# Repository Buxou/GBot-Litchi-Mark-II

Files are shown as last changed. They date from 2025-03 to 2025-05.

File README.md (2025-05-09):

# GBot-Litchi-Mark-II

Продолжение линейки Litchi – Litchi Mark II. 

[3D-моделька, чтобы покрутить.](https://myhub.autodesk360.com/ue2ddbd59/g/shares/SH286ddQT78850c0d8a4284d03fa6811be10?mode=embed)

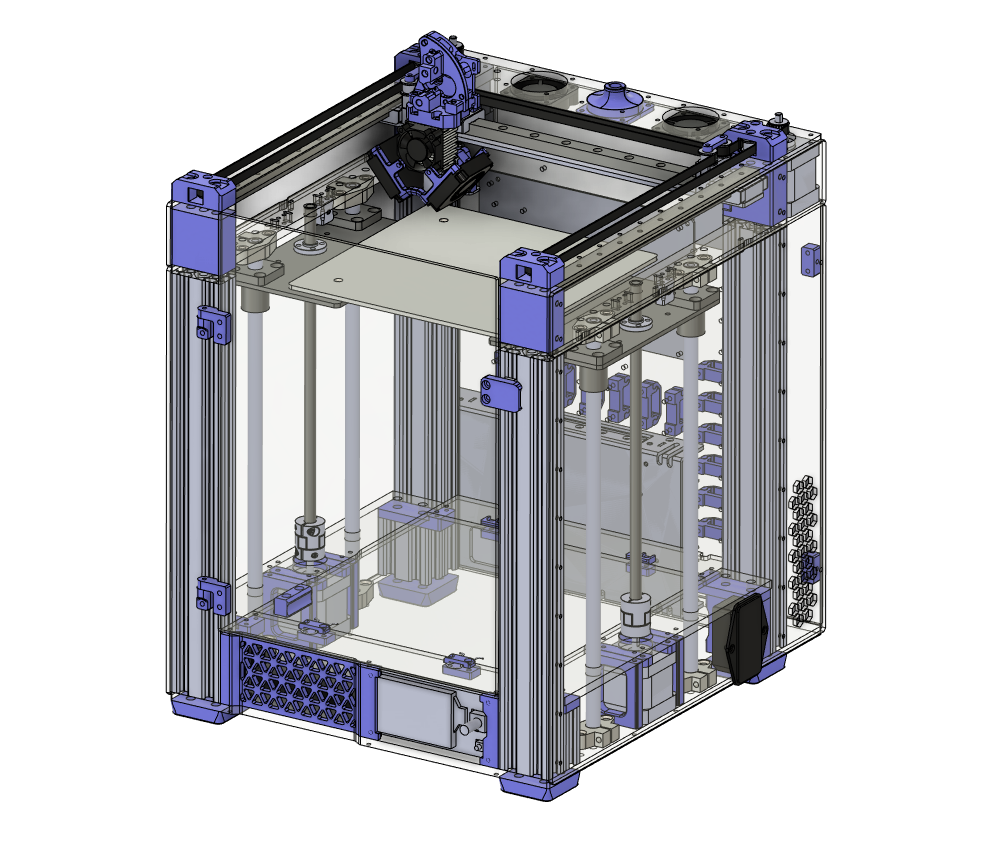
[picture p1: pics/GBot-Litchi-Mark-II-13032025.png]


## Особенности и характеристики:

- Поле 180х180х180 мм
- Габариты 340х306х420 мм
- Кинематика HBot (в перспективе CoreXY)
- Подача direct (аналог Sailfin)
- Перемещение XY – рельсы
- Перемещение Z – валы
- Датчики Холла в качестве концевиков
- Два отсека электроники: подвал/рюкзак
- Доступ к подвалу не требует переворачивания принтера
- Охлаждение рюкзака (заднего отсека) пассивное + активное
- Dual Z выравнивание сторон по концевикам
- Автокалибровка стола датчиком Beacon (карта высот)

## Корпус

Основан на констуркционном профиле 2040. Кинематика расположена на 6мм акриле, обшивка 3мм. Есть возможность установки купола, т.е. полностью закрытый корпус – пассивную термокамеру (в разработке).

## Метизы
- м6х30    8шт снизу в ножки в профиль.
- м6х18    8шт снизу в ножки в маленькие огрызки профиля\печатные детали.
- м6х85\90    8шт сверху в крепления шкивов, 85мм при верхнем портале 6мм и 90мм при верхнем портале 8мм.
- м3х10    20шт для крепления нижних правой и левой панели.
- м3х10    8шт для крепления верхних правой и левой панели.
- м3х10    14шт для крепления передней печатной панели и акриловой детали над ней и печатных деталей к ней.
- м3х10    8шт для крепления акриловой панели внутри принтера у задней стенки и крепления к ней печатных деталей для акрилового капота.
- м3х16    8шт для крепления моторов по Z.
- м3х65\70    4шт для крепления стоек рядом с моторами Z, либо переделать детали под вплавляемые гайки. Как вариант вкрутить в пластик или использовать саморезы.
- м3х10    8шт для крепления моторов на верхний портал.
- м3х20    6шт для крепления шкивов в печатных деталях по углам.
- м3х12    20шт для крепления рельс по Y.
- м3х8\10    9шт для крепления рельсы по Х, винты с длинной 10мм выглядят более надежно ибо "мяса в рельсе 3.5мм и 3мм балка Х.
- м3х8\10    4шт для крепления головы к рельсе Х при толщине верхнего портала 6мм. Толщина кронштейна в месте крепления 6мм и глубина резьбы в каретке 3.5мм, лучше взять винты длиной 10мм и проложить шайбы.
- м3х10\12    4шт для крепления головы к рельсе Х при верхрем портале в 8мм. Толщина кронштейна в месте крепления 8мм и глубина резьбы в каретке 3.5мм, лучше взять винты длиной 12мм и проложить шайбы.
- м3х6    8шт для крепления балки Х к кареткам рельс Y.
- м3х20    3шт для крепления вентилятора обдува драйверов.
- м5х16\20    16шт для крепления держателей валов оси Z. Длина 16мм для держателей валов с "тонкими ушами" в 5мм, для держаталей с толстыми ушами 20мм.

- Осторожно могут быть ошибки, просьба сверяться с 3д моделью. Позже допишу.

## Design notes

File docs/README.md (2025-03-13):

## Содержание данной секции:

(ещё не готово) **[BOM GBot Litchi Mark II.md](BOM_GBot_Litchi_Mark_II.md)** — список комплектующих

(ещё не готово) **[Fixings BOM GBot Litchi Mark II.md](Fixings_BOM_GBot_Litchi_Mark_II.md)** — расширенный список "болтов, винтов и гаек"

**[Datasheet A3144.pdf](Datasheet_A3144.pdf)** — документация на датчики Холла А3144, которые используются как концевики

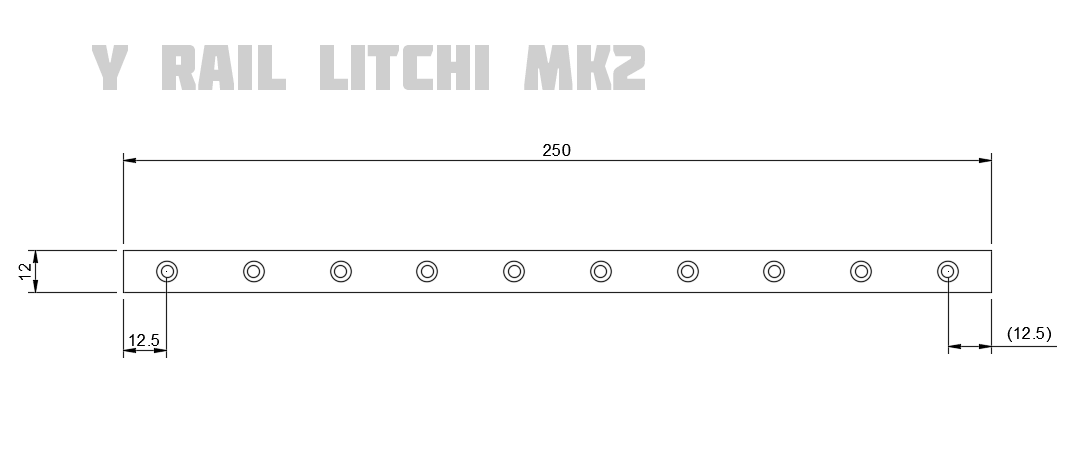
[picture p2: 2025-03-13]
docs/drawings/Y_Rail_GBot_Litchi_Mk2.png

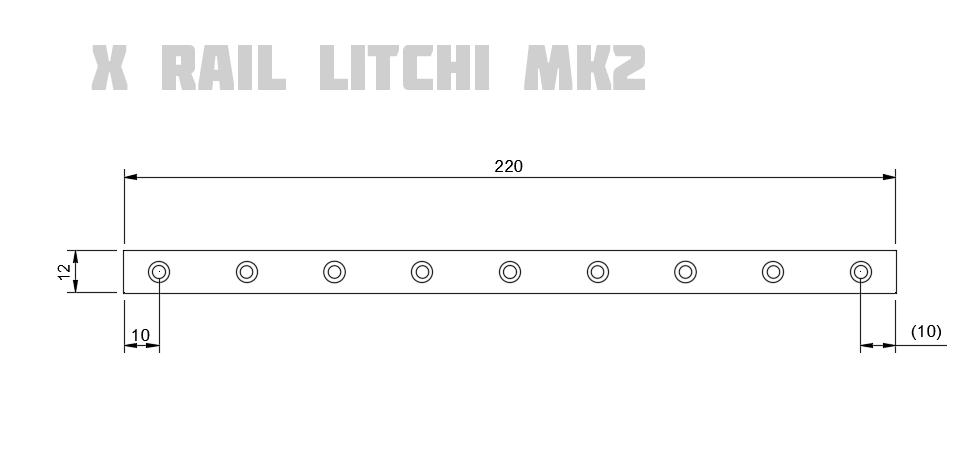
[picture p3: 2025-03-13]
docs/drawings/X_Rail_GBot_Litchi_Mk2.png

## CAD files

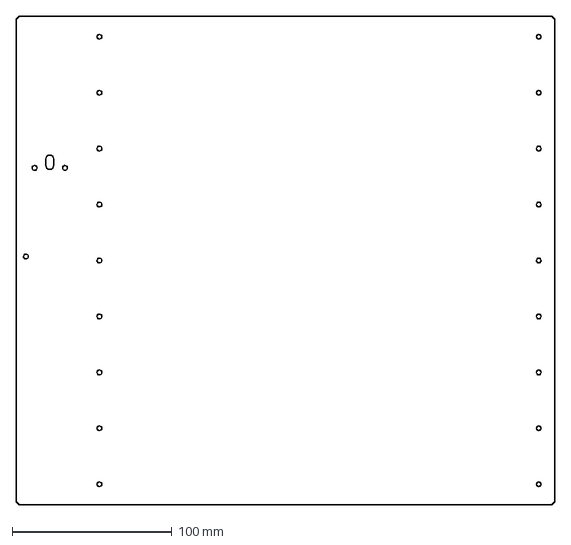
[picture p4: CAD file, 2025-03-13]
CAD/DXF/leftPanelBottom GBtLitchiMII.DXF
337.0 x 306.0 mm

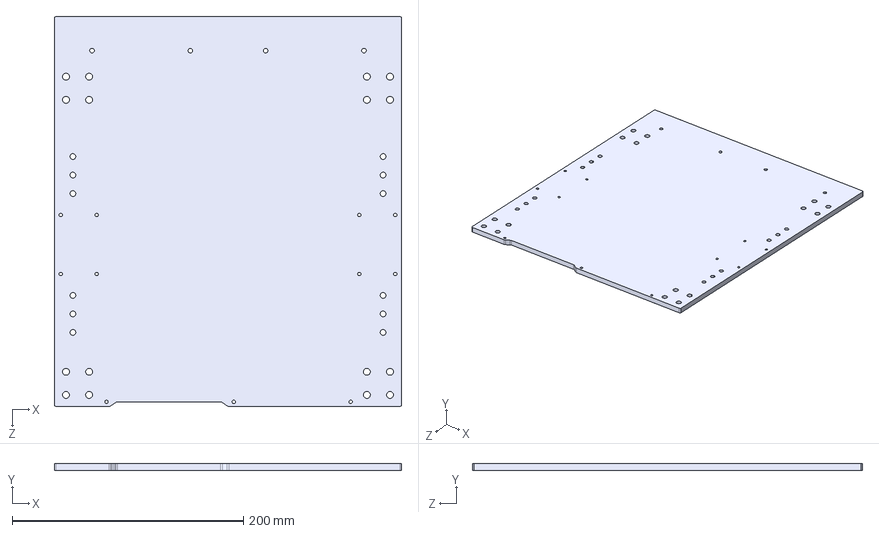
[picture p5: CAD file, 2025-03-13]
CAD/STEP/bottomPlate GBtLitchiMII.STEP
300.0 x 6.00 x 337.0 mm

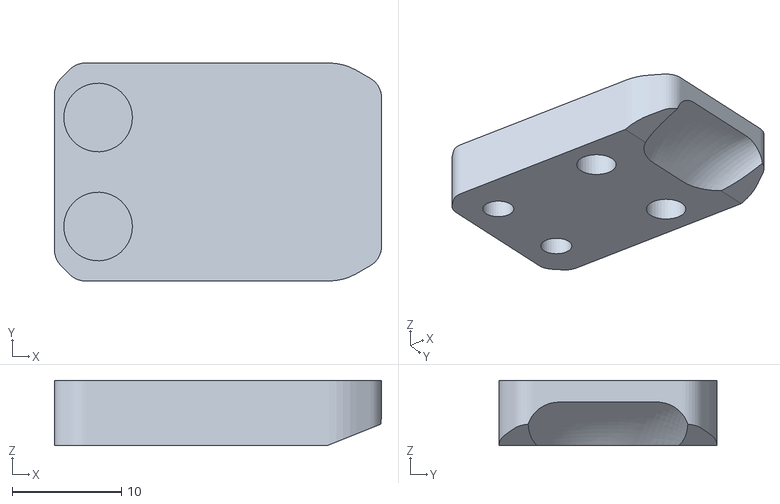
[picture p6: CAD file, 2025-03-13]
CAD/STL/doorHandle GBtLitchiMII.STL
30.0 x 20.0 x 6.00

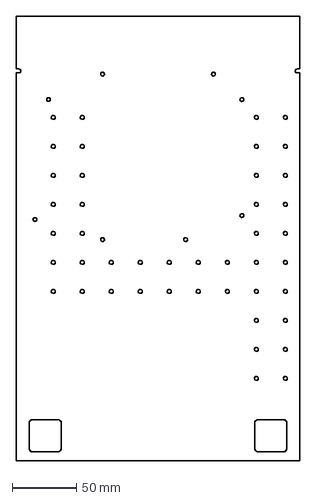
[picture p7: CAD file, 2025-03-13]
CAD/DXF/backPanel GBtLitchiMII.DXF
220.0 x 345.0 mm

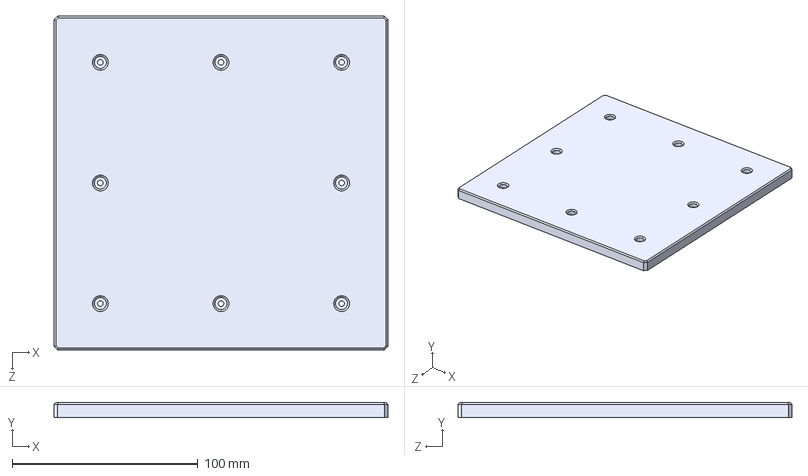
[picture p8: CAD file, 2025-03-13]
CAD/STEP/bed 9points GBtLitchiMII.STEP
180.0 x 8.00 x 180.0 mm

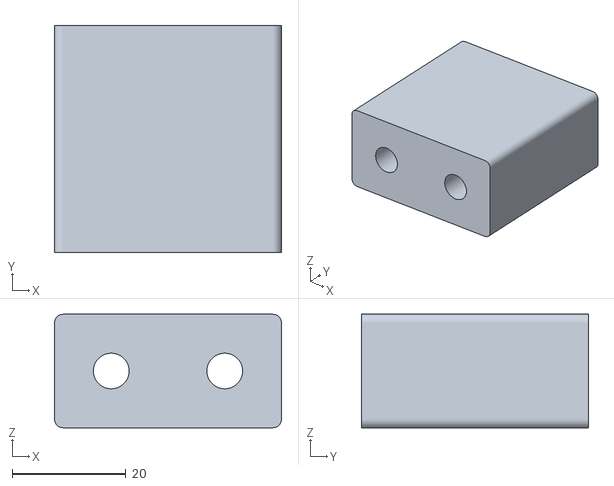
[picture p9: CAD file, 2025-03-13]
CAD/STL/frontTopPlatesSpacer GBtLitchiMII.STL
40.0 x 40.0 x 20.0

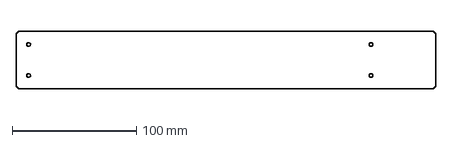
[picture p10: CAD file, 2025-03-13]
CAD/DXF/sidePanelTop GBtLitchiMII.DXF
337.0 x 46.0 mm

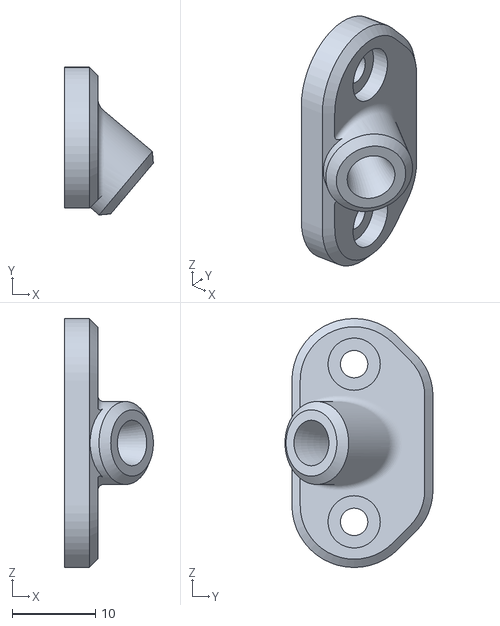
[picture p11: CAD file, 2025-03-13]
CAD/STL/bowdenGuide GBtLitchiMII.STL
10.7 x 17.8 x 30.0

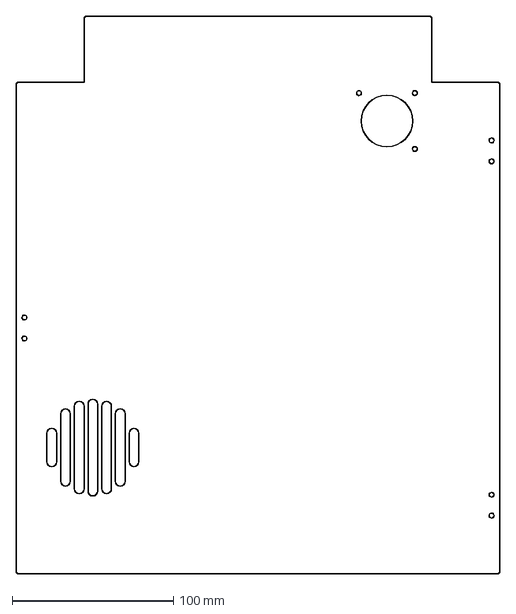
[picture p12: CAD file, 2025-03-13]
CAD/DXF/backBackPanel GBtLitchiMII.DXF
300.0 x 346.0 mm

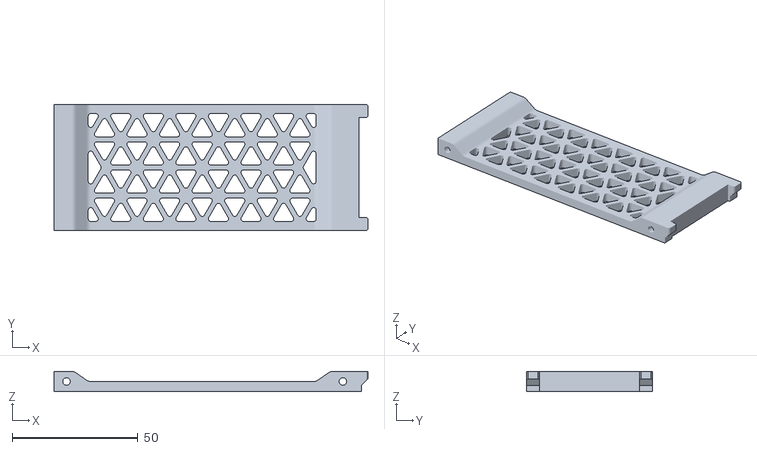
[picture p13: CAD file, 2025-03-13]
CAD/STL/leftMini12864PanelMount add1mmCut GBtLitchiMII.STL
125.0 x 50.0 x 8.00

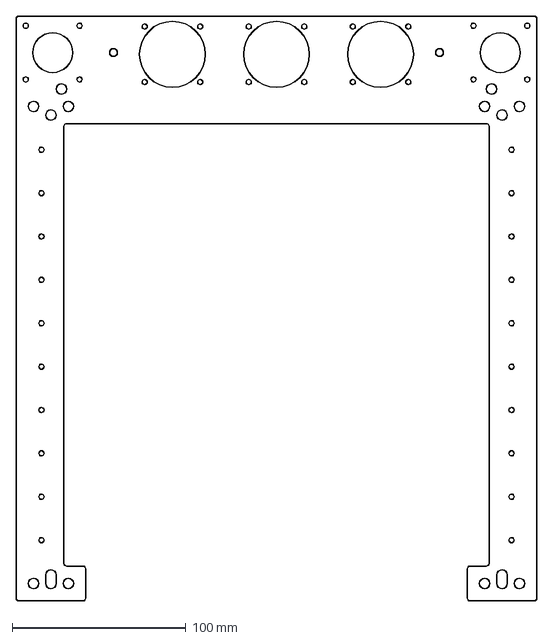
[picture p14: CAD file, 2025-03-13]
CAD/DXF/topPlate GBtLitchiMII.DXF
300.0 x 337.0 mm

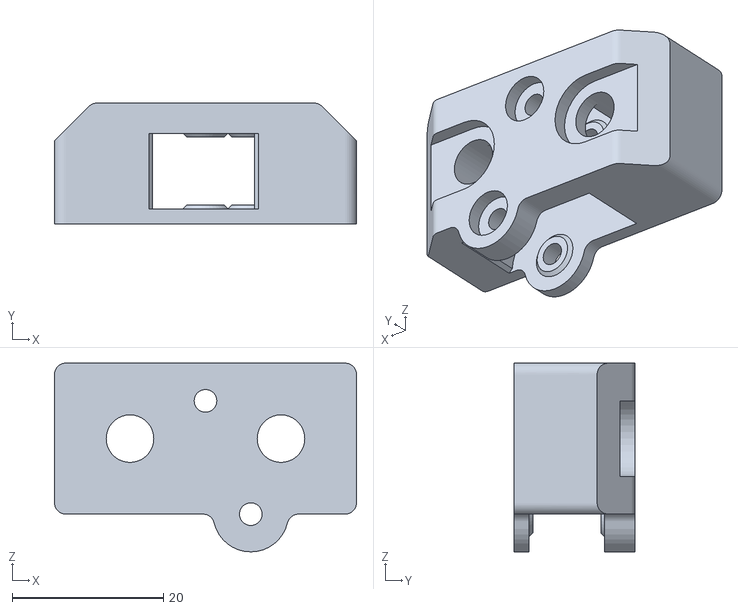
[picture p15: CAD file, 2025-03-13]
CAD/STL/idlePulleyMountRear GBtLitchiMII.STL
40.0 x 16.0 x 25.0

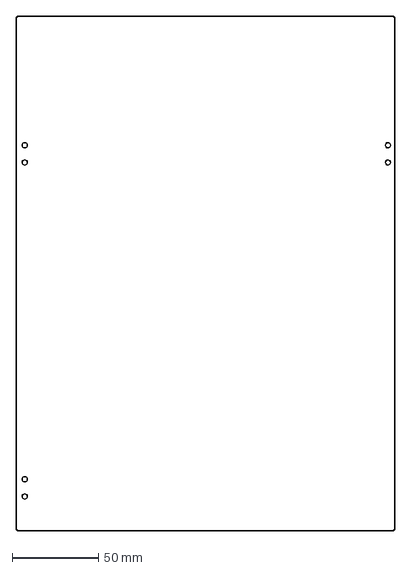
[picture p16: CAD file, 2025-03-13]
CAD/DXF/door GBtLitchiMII.DXF
220.0 x 299.0 mm

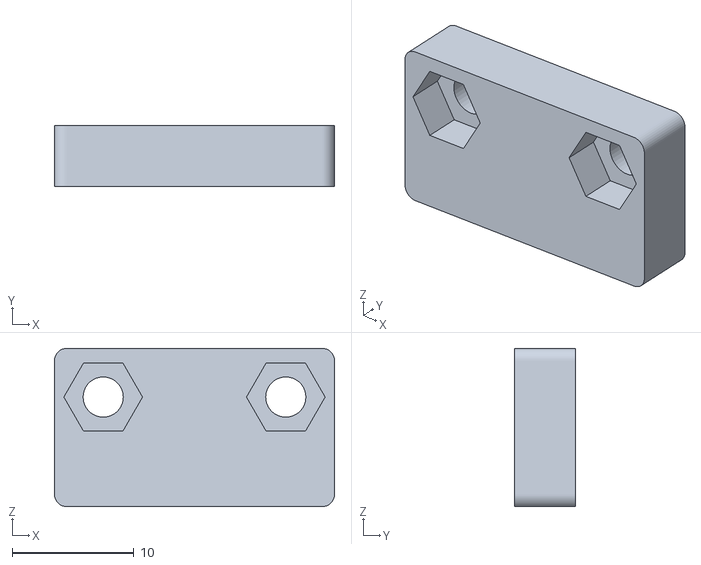
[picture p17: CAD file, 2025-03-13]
CAD/STL/electronicsCoverBottomLatchPart GBtLitchiMII.STL
23.0 x 5.00 x 13.0

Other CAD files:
CAD/STEP/bed 5points GBtLitchiMII.STEP
CAD/DXF/rightPanelBottom GBtLitchiMII.DXF
CAD/STL/backBackPanelJoint GBtLitchiMII.STL
CAD/DXF/electronicsCover GBtLitchiMII.DXF
CAD/DXF/bedMountPlate GBtLitchiMII.DXF
CAD/DXF/bottomPlate GBtLitchiMII.DXF
CAD/DXF/xRailSupport GBtLitchiMII.DXF
CAD/DXF/zShaftBottomPlate GBtLitchiMII.DXF
CAD/DXF/zShaftBottomPlateMotorSpacer GBtLitchiMII.DXF
CAD/DXF/zShaftTopPlate GBtLitchiMII.DXF
CAD/STL/backPackWireOrganizerP1.STL
CAD/STL/backPackWireOrganizerP2.STL
CAD/STL/backPanelHolderCircle GBtLitchiMII.stl
CAD/STL/beaconMount GBtLitchiMII.STL
CAD/STL/bedKnobT2 GBtLitchiMII.STL
CAD/STL/doorHandleStop GBtLitchiMII.STL
CAD/STL/doorHingeP1 GBtLitchiMII.STL
CAD/STL/doorHingeP2 GBtLitchiMII.STL
CAD/STL/electronicsCoverBottomPseudoHinge GBtLitchiMII.STL
CAD/STL/electronicsCoverHandle GBtLitchiMII.STL
CAD/STL/electronicsCoverSupportMount GBtLitchiMII.STL
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

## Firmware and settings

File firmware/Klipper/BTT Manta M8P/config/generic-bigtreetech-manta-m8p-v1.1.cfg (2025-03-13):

# This file contains common pin mappings for the BIGTREETECH Manta M8P
# To use this config, the firmware should be compiled for the
# STM32G0B1 with a "8KiB bootloader" "8 MHz crystal"
# and "USB (on PA11/PA12)" or "CAN bus (on PD12/PD13)".

# See docs/Config_Reference.md for a description of parameters.

[mcu]
serial: /dev/serial/by-id/usb-Klipper_stm32g0b1xx_22000A0011504B4633373520-if00

[printer]
kinematics: corexy
max_velocity: 300
max_accel: 3000
max_z_velocity: 5
max_z_accel: 100

# [temperature_sensor CPU]
# sensor_type: temperature_host

# [temperature_sensor MCU]
# sensor_type: temperature_mcu

[stepper_x]
step_pin: PE2
dir_pin: PB4
enable_pin: !PC11
microsteps: 16
rotation_distance: 32
endstop_pin: !PF3
position_endstop: 0
position_max: 180
homing_speed: 50

[stepper_y]
step_pin: PF12
dir_pin: PF11
enable_pin: !PB3
microsteps: 16
rotation_distance: 32
endstop_pin: !PF4
position_endstop: 168
position_max: 168
homing_speed: 50
homing_retract_dist: 5.0

[stepper_z]
step_pin: PD7
dir_pin: PD6
enable_pin: !PF10
microsteps: 16
rotation_distance: 4
#endstop_pin: probe:z_virtual_endstop # парковка по датчику уровня стола
endstop_pin: !PF5        # закомментировать, если по датчку уровня стола
position_endstop: 0.0    # закомментировать, если по датчку уровня стола
position_max: 180
homing_speed: 10
# homing_retract_dist: 5.0

[stepper_z1]
step_pin: PD3
dir_pin: PD2
enable_pin: !PD5
microsteps: 16
rotation_distance: 4
endstop_pin: !PC0      # закомментировать, если по датчку уровня стола

[extruder]
step_pin: PC9
dir_pin: !PC8
enable_pin: !PD1
microsteps: 16
rotation_distance: 23.98
gear_ratio: 50:10
nozzle_diameter: 0.400
filament_diameter: 1.750
heater_pin: PE3 # HE0
sensor_type: EPCOS 100K B57560G104F
sensor_pin: PA1 # T0
control: pid
pid_Kp=14.658 
pid_Ki=0.850 
pid_Kd=63.214
min_temp: 0
max_temp: 250

[heater_bed]
heater_pin: PB7
sensor_type: Generic 3950
sensor_pin: PA0 # TB
control = pid
pid_kp = 73.670
pid_ki = 1.742
pid_kd = 928.845
min_temp: 0
max_temp: 130

[heater_fan fan]
pin: PE6

[fan]
pin: PE0

[fan_generic enclosure1]
pin: PC12

[fan_generic enclosure2]
pin: PE5

[fan_generic driver_fan]
pin: PE4

#[heater_fan SoC_fan]
#pin: CB1:gpio79
#pin: RPI:gpio26


########################################
# TMC2209 configuration
########################################
[tmc2209 stepper_x]
uart_pin: PC10
#diag_pin: PF3
run_current: 0.800
stealthchop_threshold: 999999

[tmc2209 stepper_y]
uart_pin: PF13
#diag_pin: PF4
run_current: 0.800
stealthchop_threshold: 999999

[tmc2209 stepper_z]
uart_pin: PF9
#diag_pin: PF5
run_current: 0.650
stealthchop_threshold: 999999

[tmc2209 stepper_z1]
uart_pin: PD4
#diag_pin: PC0
run_current: 0.650
stealthchop_threshold: 999999

[tmc2209 extruder]
uart_pin: PD0
run_current: 0.300
stealthchop_threshold: 999999

[board_pins]
aliases:
    # EXP1 header
    EXP1_1=PE9, EXP1_2=PE10,
    EXP1_3=PE11, EXP1_4=PE12,
    EXP1_5=PE13, EXP1_6=PE14,    # Slot in the socket on this side
    EXP1_7=PE15, EXP1_8=PB10,
    EXP1_9=<GND>, EXP1_10=<5V>,

    # EXP2 header
    EXP2_1=PB14, EXP2_2=PB13,
    EXP2_3=PF7, EXP2_4=PB12,
    EXP2_5=PE7, EXP2_6=PB11,      # Slot in the socket on this side
    EXP2_7=PE8, EXP2_8=<RST>,
    EXP2_9=<GND>, EXP2_10=<NC>


######################################################################
# BigTreeTech mini12864 (with neopixel backlight leds)
######################################################################
[display]
lcd_type: uc1701
cs_pin: EXP1_3
a0_pin: EXP1_4
rst_pin: EXP1_5
contrast: 63
encoder_pins: ^EXP2_5, ^EXP2_3
click_pin: ^!EXP1_2
## Some micro-controller boards may require an spi bus to be specified:
# spi_bus: spi1
## Alternatively, some micro-controller boards may work with software spi:
spi_software_miso_pin: EXP2_1
spi_software_mosi_pin: EXP2_6
spi_software_sclk_pin: EXP2_2

# [output_pin beeper]
# pin: EXP1_1

[neopixel mini12864]
pin: EXP1_6
chain_count: 3
initial_RED: 0.529
initial_GREEN: 0.251
initial_BLUE: 0.549
color_order: RGB


#[bltouch]
#sensor_pin: PB2
#control_pin: PB1

# Proximity switch
#[probe]
#pin: PF6

#[output_pin ps_on_pin]
#pin: PC3

#[output_pin pc13_pin]
#pin: PC13

[neopixel left_strip]
pin: PA9
chain_count: 7
initial_RED: 1
initial_GREEN: 1
initial_BLUE: 1

[neopixel right_strip]
pin: PB15
chain_count: 7
initial_RED: 1
initial_GREEN: 1
initial_BLUE: 1

#[hall_filament_width_sensor]
#adc1: PC5
#adc2: PB0

#[adxl345]
#cs_pin: PC4
#spi_bus: spi1

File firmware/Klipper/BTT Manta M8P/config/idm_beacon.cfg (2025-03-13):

[idm]
serial: /dev/serial/by-id/usb-IDM_614e_20002C001443565537353020-if00
speed: 40.0                     #   Z probing dive speed.
lift_speed: 5.0                 #   Z probing lift speed.
backlash_comp: 0.5              #   Backlash compensation distance for removing Z backlash before measuring the sensor response.
x_offset: 0.0                   #   X offset of idm from the nozzle.
y_offset: 17.5                  #   Y offset of idm from the nozzle.
trigger_distance: 2.0           #   idm trigger distance for homing.
trigger_dive_threshold: 1.5     #   Threshold for range vs dive mode probing. Beyond `trigger_distance + trigger_dive_threshold` a dive will be used.
trigger_hysteresis: 0.006       #   Hysteresis on trigger threshold for untriggering, as a percentage of the trigger threshold.
cal_nozzle_z: 0.1               #   Expected nozzle offset after completing manual Z offset calibration.
cal_floor: 0.1                  #   Minimum z bound on sensor response measurement.
cal_ceil:5.0                    #   Maximum z bound on sensor response measurement.
cal_speed: 1.0                  #   Speed while measuring response curve.
cal_move_speed: 10.0            #   Speed while moving to position for response curve measurement.
default_model_name: default     #   Name of default idm model to load.
mesh_main_direction: x          #   Primary travel direction during mesh measurement.
#mesh_overscan: -1
#   Distance to use for direction changes at mesh line ends. Omit this setting
#   and a default will be calculated from line spacing and available travel.
mesh_cluster_size: 1    #   Radius of mesh grid point clusters.
mesh_runs: 2            #   Number of passes to make during mesh scan.

[bed_mesh]
speed: 120
mesh_min: 10, 20
mesh_max: 160, 160
probe_count: 10, 10
algorithm: bicubic
bicubic_tension: 0.2

[idm model default]
model_coef: 1.4694732456312025,
    1.9065276909006992,
    0.7810805302706562,
    0.2608384006650995,
    0.22599615775175122,
    0.5687685814677635,
    -0.05744885214262245,
    -0.5940043666132714,
    0.133069820668423,
    0.3111917643907581
model_domain: 3.2973820431625874e-07,3.3716822107660534e-07
model_range: 0.100000,5.000000
model_temp: 27.591591
model_offset: 0.00000

[bed_mesh default]
version: 1
points: 
  -0.403901, -0.318963, -0.308328, -0.294453, -0.280661, -0.267119, -0.258242, -0.244001, -0.232931, -0.232900
  -0.327508, -0.251114, -0.237005, -0.227673, -0.216501, -0.212440, -0.206182, -0.198134, -0.186310, -0.191099
  -0.285763, -0.212929, -0.206298, -0.195827, -0.190533, -0.188759, -0.188361, -0.186354, -0.182975, -0.186226
  -0.270330, -0.206246, -0.202744, -0.200393, -0.197955, -0.203156, -0.206235, -0.212824, -0.212324, -0.219209
  -0.254122, -0.189634, -0.193645, -0.196230, -0.199514, -0.203298, -0.212401, -0.216560, -0.222896, -0.233749
  -0.245798, -0.184707, -0.191609, -0.198854, -0.198802, -0.209371, -0.218353, -0.229624, -0.239691, -0.262246
  -0.248128, -0.193299, -0.203614, -0.210430, -0.219557, -0.230995, -0.248502, -0.262142, -0.276786, -0.296992
  -0.214048, -0.168825, -0.181786, -0.193771, -0.203301, -0.220706, -0.236449, -0.254977, -0.270268, -0.292410
  -0.154287, -0.111618, -0.130957, -0.144203, -0.160639, -0.178193, -0.197049, -0.212984, -0.230319, -0.254928
  -0.091348, -0.063108, -0.084415, -0.101831, -0.117577, -0.137864, -0.159011, -0.178891, -0.193829, -0.209866
x_count: 10
y_count: 10
mesh_x_pps: 2
mesh_y_pps: 2
algo: bicubic
tension: 0.2
min_x: 10.0
max_x: 160.0
min_y: 20.0
max_y: 160.0

# расскомментировать эту секцию
# если парковка по датчку уровня стола
# [safe_z_home]
# home_xy_position: 90, 90
# z_hop: 10

# [adxl345]
# cs_pin: idm:PA3
# spi_bus: spi1

# [resonance_tester]
# accel_chip: adxl345
# probe_points:
#     90, 90, 20

# [force_move]
# enable_force_move: true

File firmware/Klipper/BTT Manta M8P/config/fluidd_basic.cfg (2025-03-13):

[display_status]

[pause_resume]

[gcode_macro CANCEL_PRINT]
description: Cancel the actual running print
rename_existing: CANCEL_PRINT_BASE
gcode:
  TURN_OFF_HEATERS
  CANCEL_PRINT_BASE

[virtual_sdcard]
path: /home/biqu/printer_data/gcodes
on_error_gcode: CANCEL_PRINT

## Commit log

2025-04-03 Update README.md
    Добавил некоторое кол-во крепежа.
2025-04-03 Update README.md
    Поправил описание.
2025-04-03 Update README.md
    Добавил список метизов.
2025-04-07 Update README.md
    Добавил еще немного метизов, проверяйте.
